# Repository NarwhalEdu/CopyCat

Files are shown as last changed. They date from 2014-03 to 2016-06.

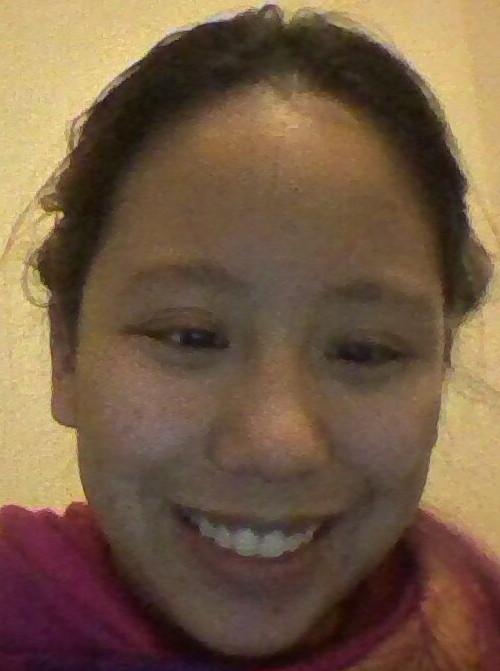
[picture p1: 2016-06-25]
vectorpaint/me.jpg

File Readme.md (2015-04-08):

NarwhalEdu CopyCat Robot (Source Files)
=========

CopyCat is a small robot arm that draws.

robot drawing nyancat 
(prototype shown)

It consists of an atmega328 microcontroller running the Arduino bootloader, three servos, a lasercut acrylic/birch box, and a 3d-printed pen holder that holds markers up to a sharpie of "fine" thickness using a set screw. 

Copycat was the physical kit paired with NarwhalEdu's first class, "Robots, Drawing, and Engineering: An Online Course," and was mailed to our kickstarter backers in February 2014. See https://www.kickstarter.com/projects/narwhaledu/robots-drawing-and-engineering-an-online-course for more information on the kickstarter.

Update (April 2015): It is accompanied by our EdX class, now released to the public for free:  https://edge.edx.org/courses/NarwhalEdu/E101/2014_Spring/info 
You will need to sign up for an Edge Edx account (any one will do).
edx screenshot

kickstarter gif

Version
----

1.0

Repository Structure
-----------

### Hardware
#### Requirements
Screwdriver, soldering iron and solder, heatshrink and hot air gun if you wish

#### Lasercut Pieces

The solidworks files are the oldest -- the folder structure may be a bit messed up as of 13 March 2014, so the assembly file may not work out of the box, but all the files are there. However, the hole sizes and other cosmetic changes may have occurred between the solidworks files and the final inkscape lasercut files.

The Lasercut-ponoko files are EXAMPLES only of how you might order the pieces from ponoko. !!We have not ordered these files from ponoko or shapeways ourselves.!!

The most accurate files, although still not fully accurate, are the inkscape .svg (exported to .pdf as well) files in Lasercut-Yubo. However, the thickness of the legs on the C and D pieces are still thinner than the final version, which has a closer-fit with piece E.

To order lasercut pieces individually, we suggest (but cannot guarantee) using inkscape to move the Yubo drawings into ponoko templates, and then filing holes that are too small or hot-gluing holes that are too big. The main reason for the uncertainty is variation in lasercutter kerf widths depending on the lasercutter, which affects the pressfits we have in our design (on the potentiometer, the servo horns, and close-fit on C/D/E pieces).

#### 3d Printed Penholder

The pen holder is 3d printed and can be ordered from shapeways. We recommend the hollow version if you are printing on shapeways, as it will save some costs.

#### Potentiometer

Additionally, one thing not shown is that we stripped and soldered the potentiometers to fit onto the I/O shield appropriately.

### Code

We'll release more code after the class ends at the end of March 2014. For now, there's some basic code up in which the servo robot arm will follow the potentiometer arm in a "copycat" configuration.

### Instructions

In the "instructions" folder you can find the bill of materials for the individual kits, complete with cost; the packing slip; and the assembly instructions. If you are building from scratch you will need not only a screwdriver but also a soldering iron and solder in order to assemble the potentiometers, which we did for the students.

Important Links
--------------
- https://www.kickstarter.com/projects/narwhaledu/robots-drawing-and-engineering-an-online-course
- http://narwhaledu.com/copycat
- http://github.com/narwhaledu/copycat

Installation
--------------
Warning: The full filesize for this repo is over 60 megabytes.

```sh
git clone [git-repo-url] copycat
cd copycat
```

License
----

Public Domain: http://creativecommons.org/publicdomain/zero/1.0/

To the extent possible under law, NarwhalEdu has waived all copyright and related or neighboring rights to CopyCat v1.0. This work is published from: United States. 

If you happen to see us in person, feel free to buy us some cheetos or tangerines.

Contact
----
opensource@narwhaledu.com

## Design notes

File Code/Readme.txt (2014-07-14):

CopyCat:
Arduino
Basic "copycat" arm functionality, using two potentiometers as inputs to control two servomotors.

basicsIK: 
Arduino
Basic inverse kinematics code, including examples of how to program a circle and a line.

paint:
Processing
A graphical user interface for drawing and sending commands over serial to a plugged-in Arduino running serialdraw.

serialdraw:
Arduino
Code to accept x,y commands from Processing and turn them into theta values so that the robot arm may draw them.

Inverse Kinematics explanation:
See trig.png, as well as
http://www.instructables.com/id/Robotic-Arm-with-Servo-Motors/step5/Plug-it-in-and-Write-some-code/
as well as
http://www.eng.utah.edu/~cs5310/chapters.html (uh oh! July 2014: Files now locked by password and not accessible)
Also.
"if this elbowup/down stuff is coming out of nowhere -- basically there are two combinations of theta 1 and theta 2 that will work for any given x,y coordinate and you just pick whether you want the elbow up or down solution)"
The code in basicIK.ino should be understandable after reading these resources.

For mapping the working envelope of the arm, please see the python file workingenv.py --> see workingenvelope.png for what the output should look like (generated using ipython).

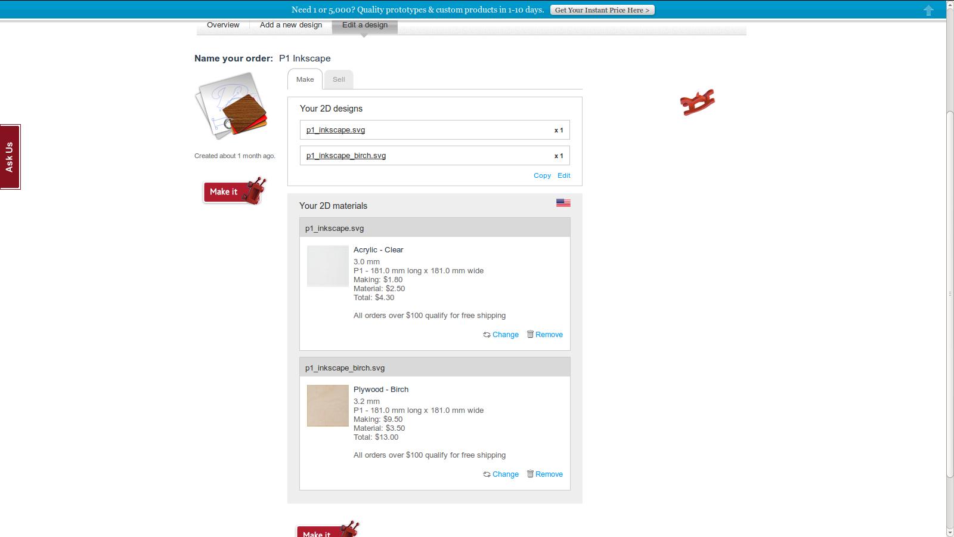
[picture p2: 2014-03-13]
Hardware/Lasercut-Ponoko-Examples/ponoko.jpg

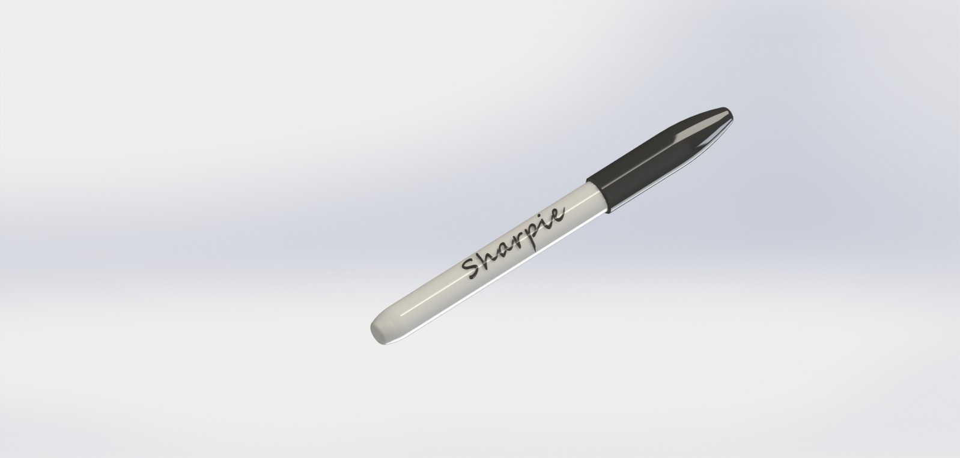
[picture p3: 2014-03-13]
Hardware/pen_holder/sharpie-brand-marker-pen/Renderings/Sharpie render20120321-19804-l9pclu.JPG

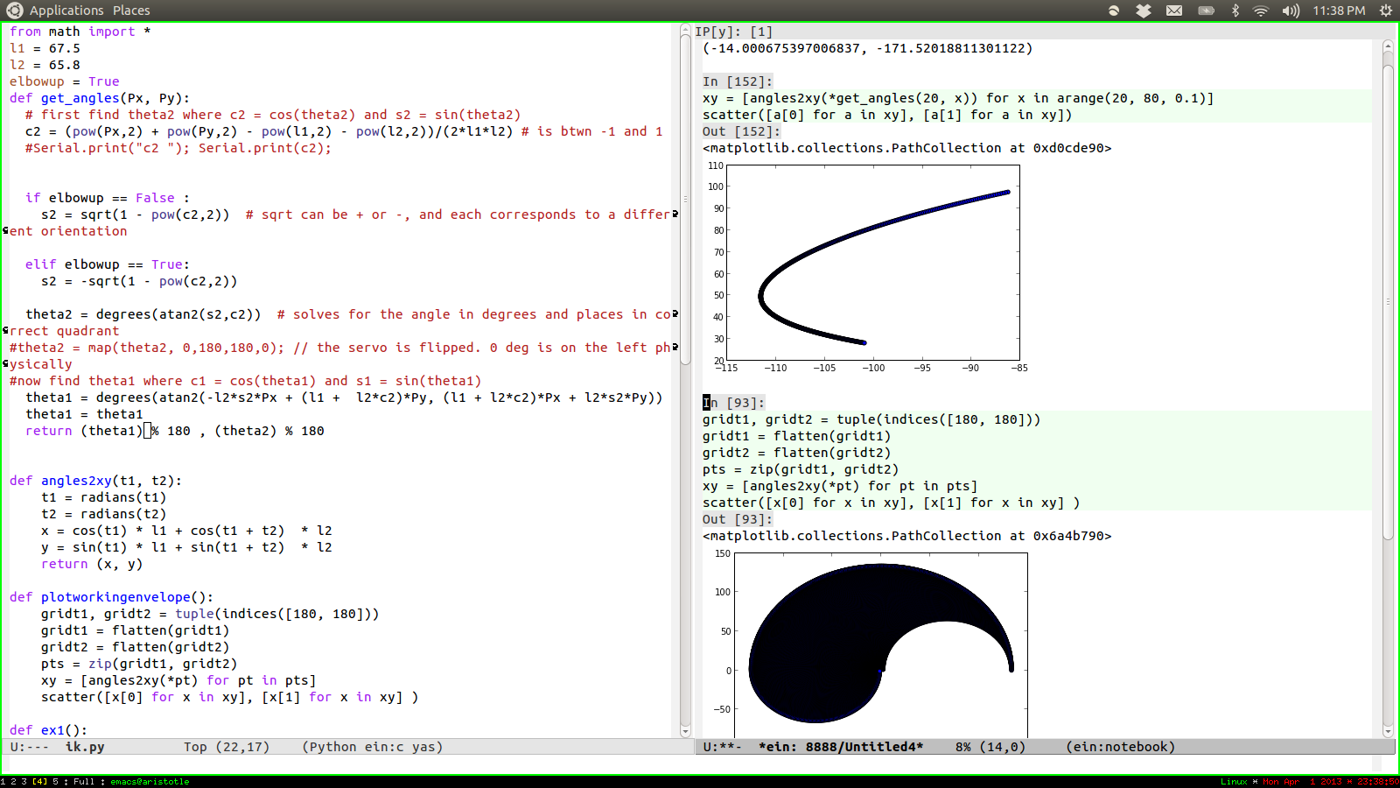
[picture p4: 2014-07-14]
Code/workingenvelope.png

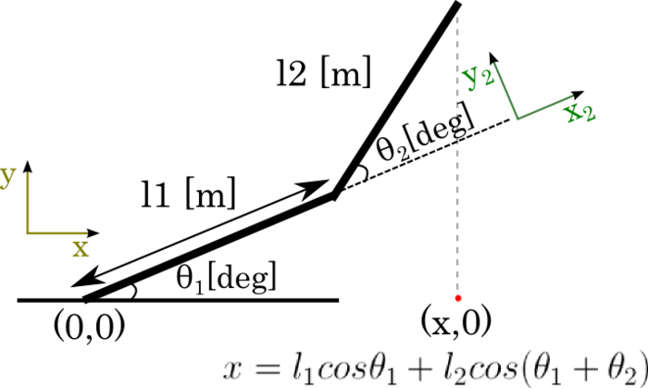
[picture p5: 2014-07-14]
Code/trig.png

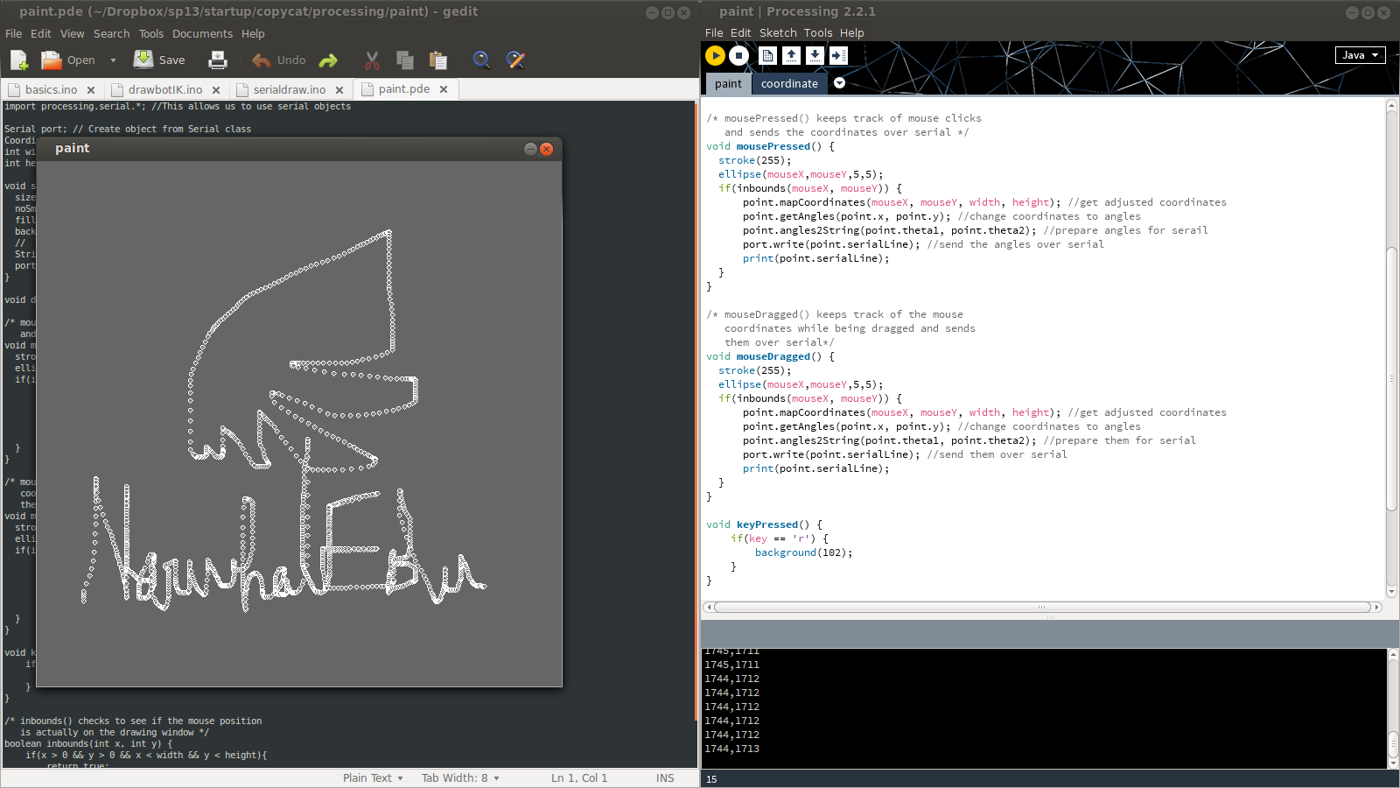
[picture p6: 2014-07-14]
Code/serialdraw+paint.png

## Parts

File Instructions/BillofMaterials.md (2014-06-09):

<table>
<col width="11%" />
<col width="11%" />
<col width="11%" />
<col width="11%" />
<col width="11%" />
<col width="11%" />
<col width="11%" />
<col width="11%" />
<col width="11%" />
<tbody>
<tr class="odd">
<td align="left"></td>
<td align="left"></td>
<td align="left"></td>
<td align="left"></td>
<td align="left"></td>
<td align="left"></td>
<td align="left"></td>
<td align="left"></td>
<td align="left"></td>
</tr>
<tr class="even">
<td align="left"><p>.</p></td>
<td align="left">what</td>
<td align="left">Supplier</td>
<td align="left">Bulk Website</td>
<td align="left">Website for Individual Kit Cost / Part number</td>
<td align="left">Cost</td>
<td align="left">Quantity needed</td>
<td align="left"></td>
<td align="left"></td>
</tr>
<tr class="odd">
<td align="left"><p>.</p></td>
<td align="left">ES08DE</td>
<td align="left">EMAX</td>
<td align="left"><a href="https://www.google.com/url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">http://www.emaxmodel.com/views.asp?hw_id=1247</a></td>
<td align="left"><a href="https://www.google.com/url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">http://www.banggood.com/Wholesale-Emax-ES08DE-Digital-Micro-Servo-For-250-450-Helis-Airplanes-p-68709.html</a></td>
<td align="left">$17.48</td>
<td align="left">4</td>
<td align="left"></td>
<td align="left"></td>
</tr>
<tr class="even">
<td align="left"><p>.</p></td>
<td align="left">ES08DE long screws</td>
<td align="left">EMAX</td>
<td align="left">not available for purchase individually</td>
<td align="left">http://www.mcmaster.com/#90380a008/=qb8znh Mcmaster part #90380A008 is roughly equivalent to the EMAX screws</td>
<td align="left">$3.50</td>
<td align="left">7 out of box of 50</td>
<td align="left"></td>
<td align="left"></td>
</tr>
<tr class="odd">
<td align="left"><p>.</p></td>
<td align="left"></td>
<td align="left"></td>
<td align="left"></td>
<td align="left"></td>
<td align="left"></td>
<td align="left"></td>
<td align="left"></td>
<td align="left"></td>
</tr>
<tr class="even">
<td align="left"><p>.</p></td>
<td align="left">Potentiometer cables</td>
<td align="left">Pololu</td>
<td align="left"><a href="https://www.google.com/url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">http://www.pololu.com/product/780</a></td>
<td align="left"></td>
<td align="left">$2.49</td>
<td align="left">1</td>
<td align="left"></td>
<td align="left"></td>
</tr>
<tr class="odd">
<td align="left"><p>.</p></td>
<td align="left"></td>
<td align="left"></td>
<td align="left"></td>
<td align="left"></td>
<td align="left"></td>
<td align="left"></td>
<td align="left"></td>
<td align="left"></td>
</tr>
<tr class="even">
<td align="left"><p>.</p></td>
<td align="left"></td>
<td align="left"></td>
<td align="left"></td>
<td align="left"></td>
<td align="left"></td>
<td align="left"></td>
<td align="left"></td>
<td align="left"></td>
</tr>
<tr class="odd">
<td align="left"><p>.</p></td>
<td align="left">Servo Extension Cable 300mm</td>
<td align="left">RobotMesh</td>
<td align="left"><a href="https://www.google.com/url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">http://www.robotmesh.com/servo-extension-cable-300mm</a></td>
<td align="left"></td>
<td align="left">$1.40</td>
<td align="left">2</td>
<td align="left"></td>
<td align="left"></td>
</tr>
<tr class="even">
<td align="left"><p>.</p></td>
<td align="left">Servo Extension Cable 150mm</td>
<td align="left">RobotMesh</td>
<td align="left"><a href="https://www.google.com/url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">http://www.robotmesh.com/servo-extension-cable-150mm</a></td>
<td align="left"></td>
<td align="left">$0.60</td>
<td align="left">1</td>
<td align="left"></td>
<td align="left"></td>
</tr>
<tr class="odd">
<td align="left"><p>.</p></td>
<td align="left"></td>
<td align="left"></td>
<td align="left"></td>
<td align="left"></td>
<td align="left"></td>
<td align="left"></td>
<td align="left"></td>
<td align="left"></td>
</tr>
<tr class="even">
<td align="left"><p>.</p></td>
<td align="left">POTENTIOMETER ROTARY 5K OHM 16MM SOLDER</td>
<td align="left">Digikey</td>
<td align="left"><a href="https://www.google.com/url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">http://www.digikey.com/product-detail/en/P160KNP-0FC25B5K/987-1311-ND/2408888</a></td>
<td align="left">987-1311-ND</td>
<td align="left">$1.68</td>
<td align="left">2</td>
<td align="left"></td>
<td align="left"></td>
</tr>
<tr class="odd">
<td align="left"><p>.</p></td>
<td align="left"></td>
<td align="left"></td>
<td align="left"></td>
<td align="left"></td>
<td align="left"></td>
<td align="left"></td>
<td align="left"></td>
<td align="left"></td>
</tr>
<tr class="even">
<td align="left"><p>.</p></td>
<td align="left">Zinc-pltd Stl Pan Head Phillips Machine Screw, 4-40 Thread, 1/2&quot; Length x 100</td>
<td align="left">Mcmaster</td>
<td align="left"><a href="https://www.google.com/url?q=http://mcmaster.com&amp;usd=2&amp;usg=ALhdy2_r-PfuAHiMmXkCKGf9Mx1Ry3E_oQ">mcmaster.com</a></td>
<td align="left">90272A110</td>
<td align="left">$1.63</td>
<td align="left">13 needed out of box of 100</td>
<td align="left"></td>
<td align="left"></td>
</tr>
<tr class="odd">
<td align="left"><p>.</p></td>
<td align="left">Zinc-plated Steel Machine Screw Hex Nut, 4-40 Thread Size, 1/4&quot; Width, 3/32&quot; Height x 100</td>
<td align="left">Mcmaster</td>
<td align="left"><a href="https://www.google.com/url?q=http://mcmaster.com&amp;usd=2&amp;usg=ALhdy2_r-PfuAHiMmXkCKGf9Mx1Ry3E_oQ">mcmaster.com</a></td>
<td align="left">90480A005</td>
<td align="left">$0.81</td>
<td align="left">21 needed out of box of 100</td>
<td align="left"></td>
<td align="left"></td>
</tr>
<tr class="even">
<td align="left"><p>.</p></td>
<td align="left">Zinc-Plated Steel Type A SAE Flat Washer, Number 2 Screw Size, 7/32&quot; OD, .01&quot;-.03&quot; Thick</td>
<td align="left">Mcmaster</td>
<td align="left"><a href="https://www.google.com/url?q=http://mcmaster.com&amp;usd=2&amp;usg=ALhdy2_r-PfuAHiMmXkCKGf9Mx1Ry3E_oQ">mcmaster.com</a></td>
<td align="left">90126A501</td>
<td align="left">$1.19</td>
<td align="left">1 needed out of box of 100</td>
<td align="left"></td>
<td align="left"></td>
</tr>
<tr class="odd">
<td align="left"><p>.</p></td>
<td align="left"></td>
<td align="left"></td>
<td align="left"></td>
<td align="left"></td>
<td align="left"></td>
<td align="left"></td>
<td align="left"></td>
<td align="left"></td>
</tr>
<tr class="even">
<td align="left"><p>.</p></td>
<td align="left">birch pieces</td>
<td align="left">Ponoko Lasercut Quote</td>
<td align="left"><a href="https://www.google.com/url?q=http://ponoko.com&amp;usd=2&amp;usg=ALhdy29cn-jdru5WrcO2noldjQy0oRjBWA">ponoko.com</a></td>
<td align="left"></td>
<td align="left">$13.00</td>
<td align="left"></td>
<td align="left"></td>
<td align="left"></td>
</tr>
<tr class="odd">
<td align="left"><p>.</p></td>
<td align="left">acrylic pieces</td>
<td align="left">Ponoko Lasercut Quote</td>
<td align="left"><a href="https://www.google.com/url?q=http://ponoko.com&amp;usd=2&amp;usg=ALhdy29cn-jdru5WrcO2noldjQy0oRjBWA">ponoko.com</a></td>
<td align="left"></td>
<td align="left">$4.30</td>
<td align="left"></td>
<td align="left"></td>
<td align="left"></td>
</tr>
<tr class="even">
<td align="left"><p>.</p></td>
<td align="left"></td>
<td align="left"></td>
<td align="left"></td>
<td align="left"></td>
<td align="left"></td>
<td align="left"></td>
<td align="left"></td>
<td align="left"></td>
</tr>
<tr class="odd">
<td align="left"><p>.</p></td>
<td align="left">3d print pen holder</td>
<td align="left">Shapeways Quote</td>
<td align="left"><a href="https://www.google.com/url?q=http://shapeways.com&amp;usd=2&amp;usg=ALhdy2_YYUwusA8m6Woy5YYOLUOF8yBiEw">shapeways.com</a></td>
<td align="left"></td>
<td align="left">$7.30</td>
<td align="left"></td>
<td align="left"></td>
<td align="left"></td>
</tr>
<tr class="even">
<td align="left"><p>.</p></td>
<td align="left"></td>
<td align="left"></td>
<td align="left"></td>
<td align="left"></td>
<td align="left"></td>
<td align="left"></td>
<td align="left"></td>
<td align="left"></td>
</tr>
<tr class="odd">
<td align="left"><p>.</p></td>
<td align="left">Nano carrier Board</td>
<td align="left">iTeadstudio</td>
<td align="left"><a href="https://www.google.com/url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">http://imall.iteadstudio.com/im120417016.html</a></td>
<td align="left"></td>
<td align="left">$9.90</td>
<td align="left"></td>
<td align="left"></td>
<td align="left"></td>
</tr>
<tr class="even">
<td align="left"><p>.</p></td>
<td align="left">Micro USB</td>
<td align="left">iTeadstudio</td>
<td align="left"><a href="https://www.google.com/url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">http://imall.iteadstudio.com/im130416001.html</a></td>
<td align="left"></td>
<td align="left">$1.20</td>
<td align="left"></td>
<td align="left"></td>
<td align="left"></td>
</tr>
<tr class="odd">
<td align="left"><p>.</p></td>
<td align="left">7.5V 1A wallwart</td>
<td align="left">iTeadstudio</td>
<td align="left"><a href="https://www.google.com/url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">http://imall.iteadstudio.com/power/im120718002.html</a></td>
<td align="left"></td>
<td align="left">$2.90</td>
<td align="left"></td>
<td align="left"></td>
<td align="left"></td>
</tr>
<tr class="even">
<td align="left"><p>.</p></td>
<td align="left">Nano microcontroller</td>
<td align="left">iTeadstudio</td>
<td align="left"><a href="https://www.google.com/url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">http://imall.iteadstudio.com/development-platform/arduino/im130615004.html</a></td>
<td align="left"></td>
<td align="left">$5.00</td>
<td align="left"></td>
<td align="left"></td>
<td align="left"></td>
</tr>
<tr class="odd">
<td align="left"><p>.</p></td>
<td align="left"></td>
<td align="left"></td>
<td align="left"></td>
<td align="left"></td>
<td align="left"></td>
<td align="left"></td>
<td align="left"></td>
<td align="left"></td>
</tr>
<tr class="even">
<td align="left"><p>.</p></td>
<td align="left">Boxes</td>
<td align="left">ULINE</td>
<td align="left"><a href="https://www.google.com/url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">http://www.uline.com/Product/Detail/S-16947/Indestructo-Literature-Mailers/10-x-4-x-4-White-Tab-Locking-Literature-Mailers</a></td>
<td align="left"></td>
<td align="left"></td>
<td align="left">These cost $0.92 each (if bought in quantity 50)</td>
<td align="left"></td>
<td align="left"></td>
</tr>
<tr class="odd">
<td align="left"><p>.</p></td>
<td align="left"></td>
<td align="left"></td>
<td align="left"></td>
<td align="left"></td>
<td align="left"></td>
<td align="left"></td>
<td align="left"></td>
<td align="left"></td>
</tr>
<tr class="even">
<td align="left"><p>.</p></td>
<td align="left">#1 Screwdriver</td>
<td align="left">any hardware store</td>
<td align="left"></td>
<td align="left"></td>
<td align="left">$1.00</td>
<td align="left"></td>
<td align="left"></td>
<td align="left"></td>
</tr>
<tr class="odd">
<td align="left"><p>.</p></td>
<td align="left"></td>
<td align="left"></td>
<td align="left"></td>
<td align="left"></td>
<td align="left"></td>
<td align="left"></td>
<td align="left"></td>
<td align="left"></td>
</tr>
<tr class="even">
<td align="left"><p>.</p></td>
<td align="left"></td>
<td align="left"></td>
<td align="left"></td>
<td align="left"></td>
<td align="left"></td>
<td align="left">Direct cost (NOT including shipping):</td>
<td align="left">40% profit model, aka 66% markup:</td>
<td align="left">See: http://www.longtail.com/the_long_tail/2009/01/a-business-mode.html</td>
</tr>
<tr class="odd">
<td align="left"><p>.</p></td>
<td align="left"></td>
<td align="left"></td>
<td align="left"></td>
<td align="left"></td>
<td align="left"></td>
<td align="left">$75.38</td>
<td align="left">$125.1308</td>
<td align="left"></td>
</tr>
</tbody>
</table>

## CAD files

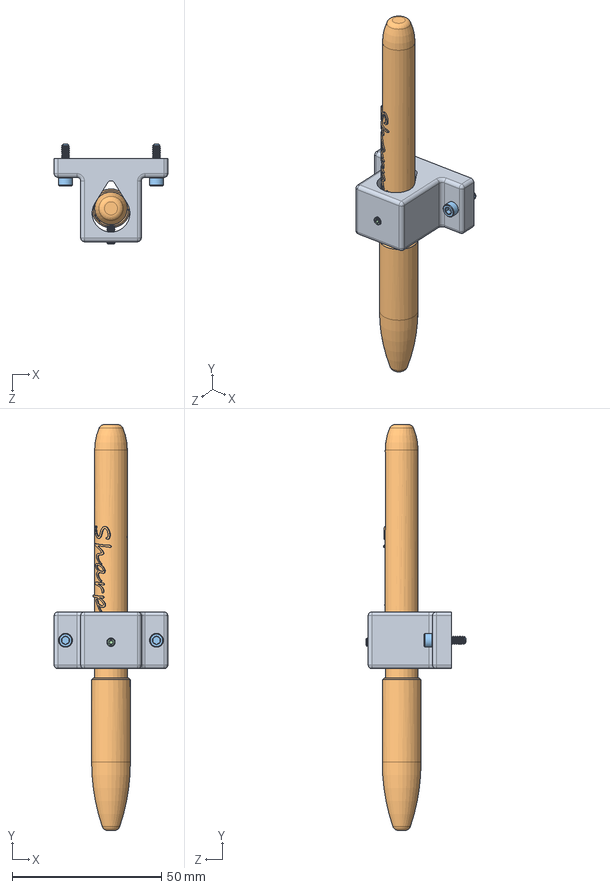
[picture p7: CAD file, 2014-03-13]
Hardware/pen_holder/pen_holder_assembly.SLDASM
38.1 x 136.0 x 33.4 mm
pen_holder
Sharpie Marker v1.0
4-40x0.4375_thumbscrew x 2
4-40x.25 set screw

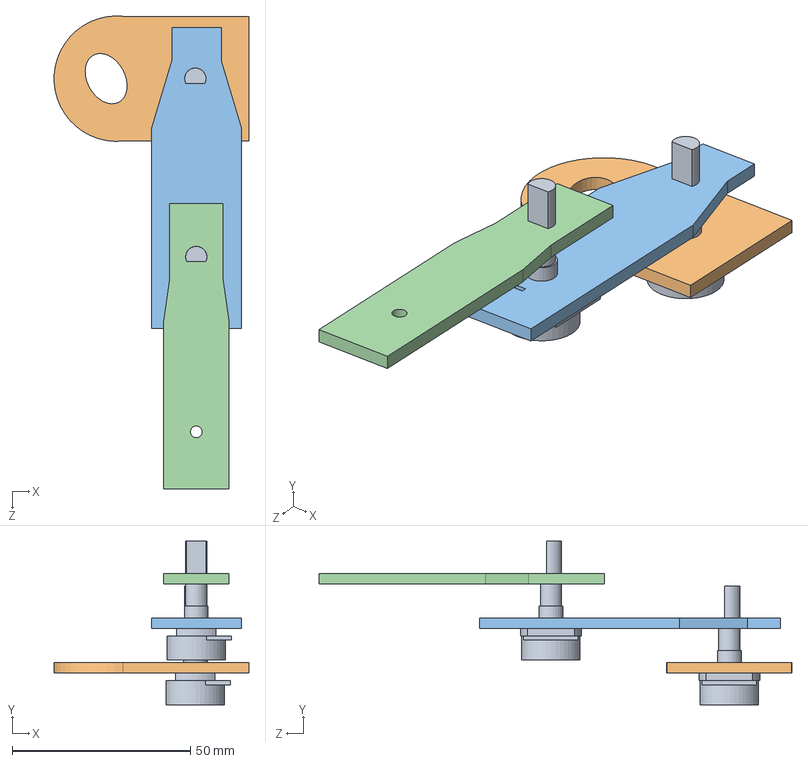
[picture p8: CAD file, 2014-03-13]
Hardware/Solidworks/potarm-Assem.SLDASM
54.6 x 45.8 x 132.6 mm
pot x 2
potbase
l1-pot
l2-pot

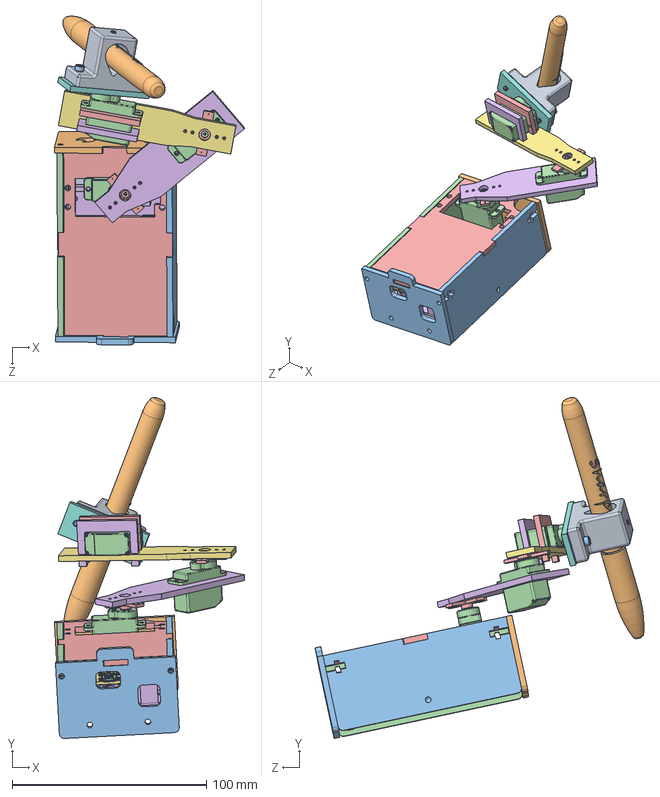
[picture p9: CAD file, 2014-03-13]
Hardware/Solidworks/Assem2.SLDASM
97.9 x 175.6 x 169.4 mm
box_bottom
4-40 Standoff 1_4 x 3
box_sides3
box_sides4
box_lid
iteadboard
nano-board
2pin_header__02 x 3
15pin_header__ x 2
atmega328
ftdi FT232rl
smt_resistor222 x 5
led x 4
16mhz crystal - measured
MINIUSBSHELL
MINIUSBCORE
MINI USB CONTACT x 5
MINI USB SOLDER
cap106C x 2
reset core
reset shell
nano - reg
NANO DIODE
189 RESISTOR PACK
102 RESISTOR PACK
box_front2
box_back2
Emax ES08A x 3
cross-horn x 2
l1
l2
penpiece
pen_holder
Sharpie Marker v1.0
4-40x0.4375_thumbscrew x 2
4-40x.25 set screw
ubracket-holes
ubracket-noholes

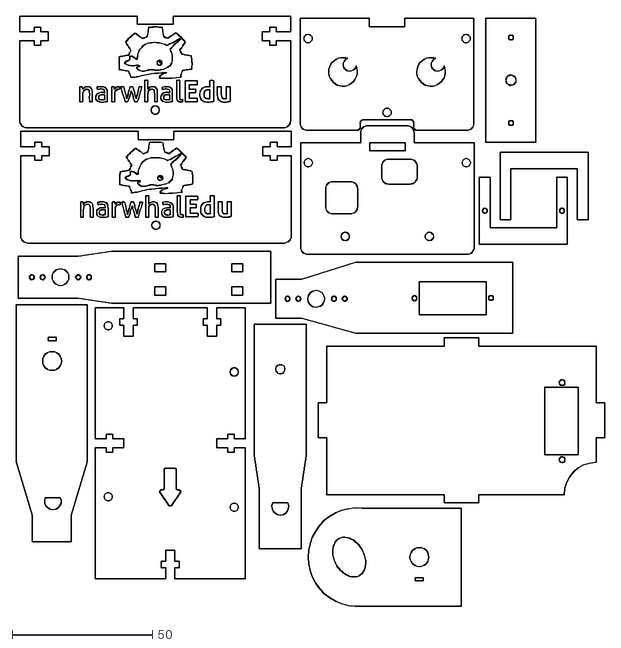
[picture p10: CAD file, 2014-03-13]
Hardware/DXF/allparts.DXF
209.7 x 211.1

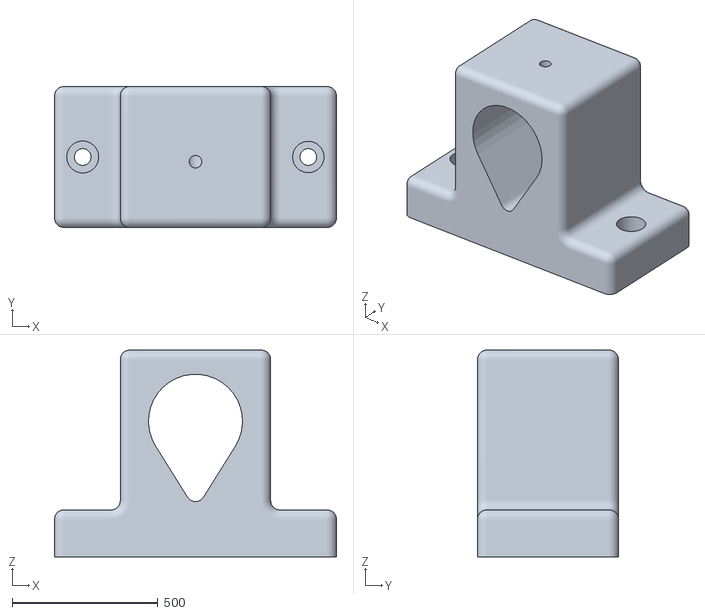
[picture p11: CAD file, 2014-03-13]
Hardware/pen_holder/penholderhollow_fixed.stl
967.7 x 483.9 x 709.7

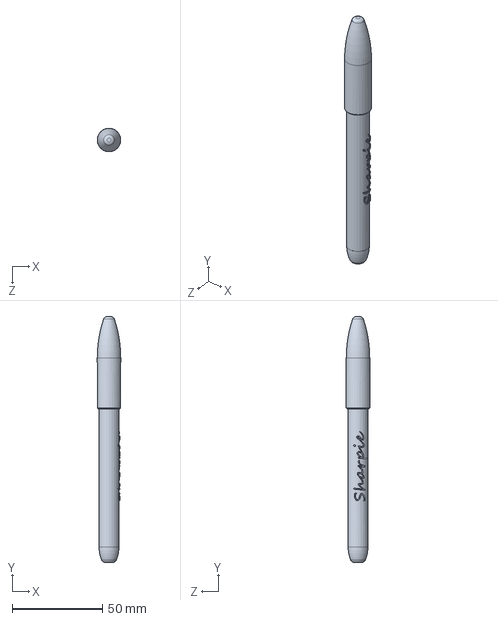
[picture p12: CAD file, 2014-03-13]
Hardware/pen_holder/sharpie-brand-marker-pen/Sharpie Marker v1.0.SLDPRT
13.0 x 136.0 x 13.0 mm

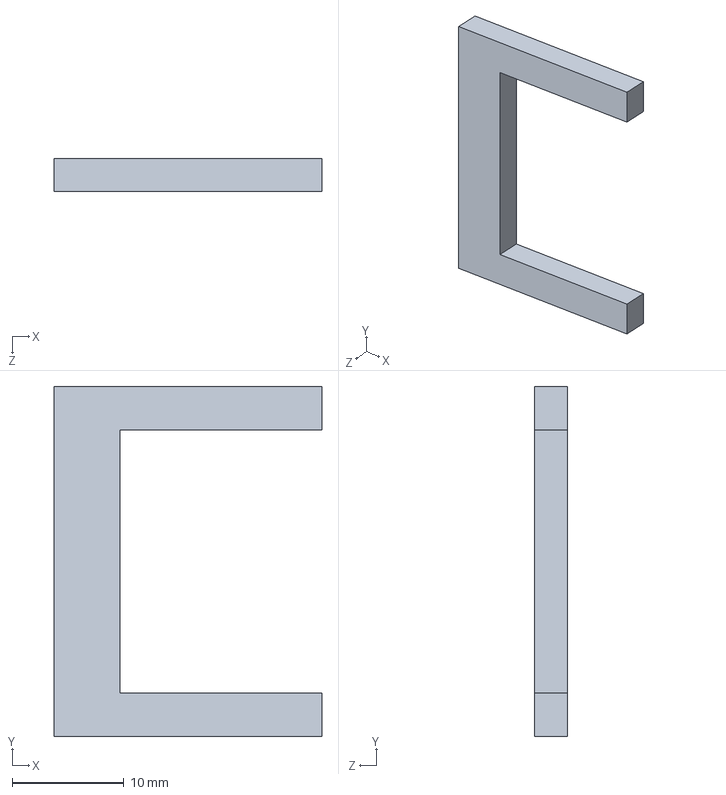
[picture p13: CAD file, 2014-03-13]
Hardware/Solidworks/ubracket-noholes.SLDPRT
24.0 x 31.4 x 3.00 mm

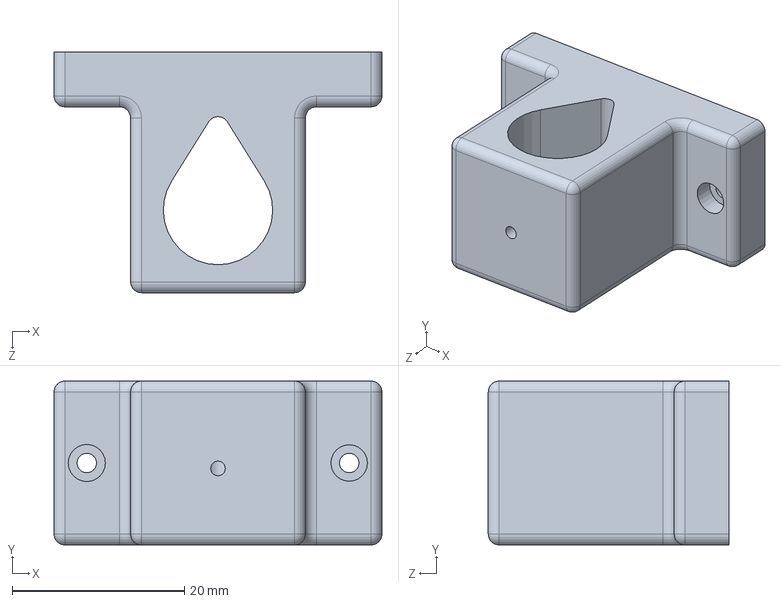
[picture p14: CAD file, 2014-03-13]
Hardware/pen_holder/pen_holder.SLDPRT
38.1 x 19.1 x 27.9 mm

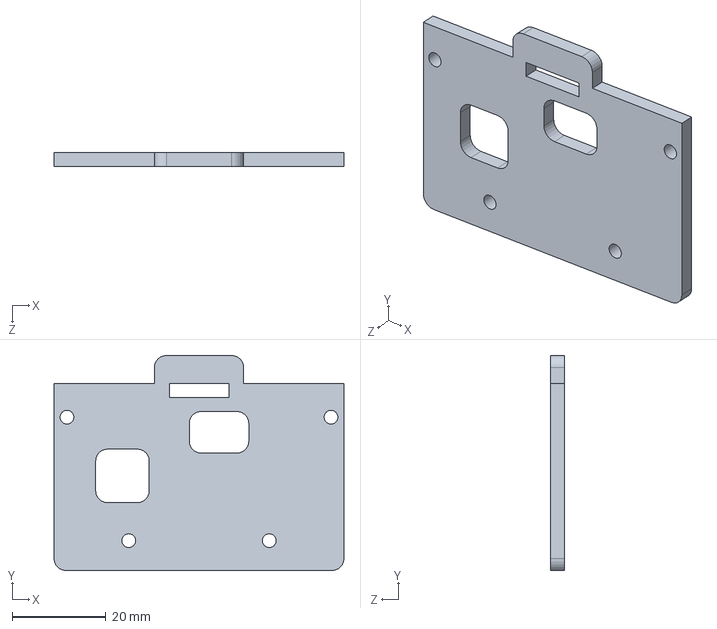
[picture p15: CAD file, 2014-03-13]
Hardware/Solidworks/box_back2.SLDPRT
61.9 x 45.9 x 3.00 mm

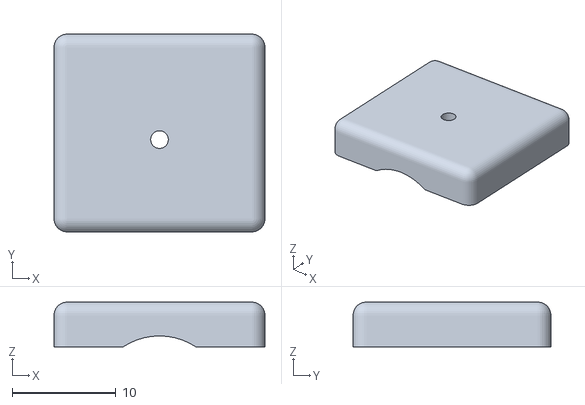
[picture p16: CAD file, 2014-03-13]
Hardware/pen_holder/pen_holder_top.STL
20.3 x 19.1 x 4.32

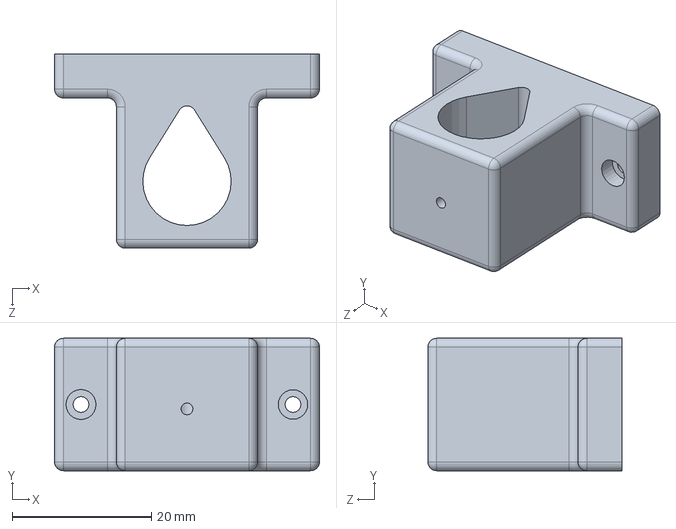
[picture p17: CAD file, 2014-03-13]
Hardware/pen_holder/pen_holder_hollow.SLDPRT
38.1 x 19.1 x 27.9 mm

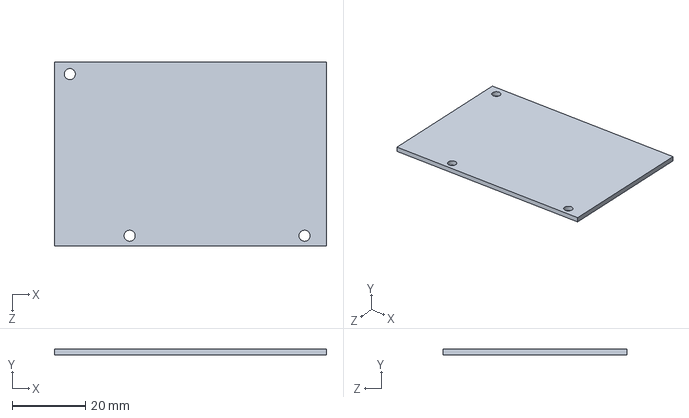
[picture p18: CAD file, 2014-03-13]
Hardware/Solidworks/io_board.SLDPRT
74.4 x 1.60 x 50.3 mm

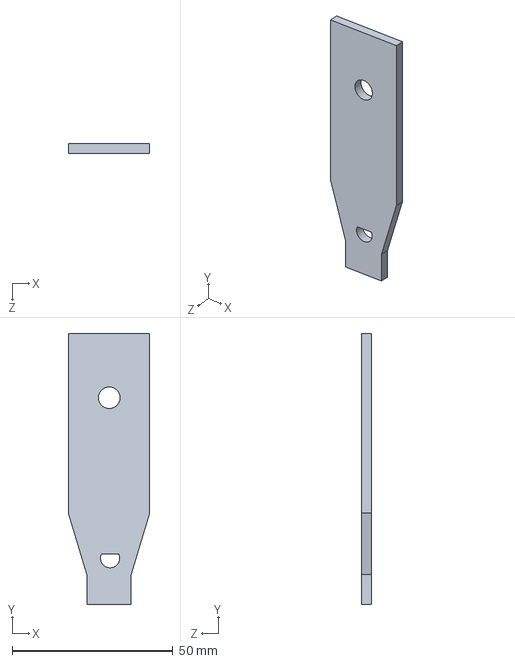
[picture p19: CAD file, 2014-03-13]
Hardware/Solidworks/l1-pot.SLDPRT
25.3 x 84.4 x 3.00 mm

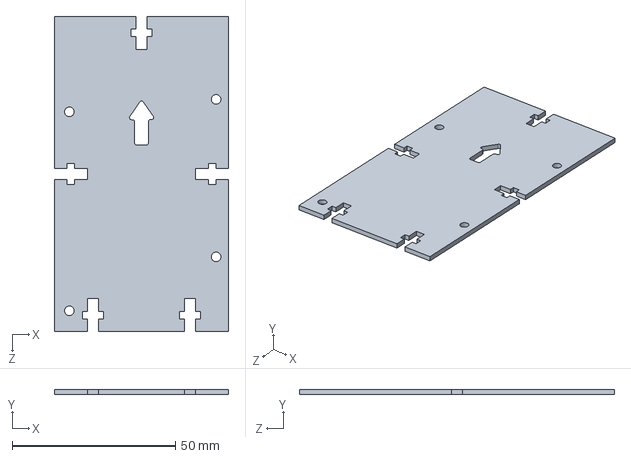
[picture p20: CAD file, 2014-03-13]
Hardware/Solidworks/box_bottom.SLDPRT
53.3 x 1.60 x 96.5 mm

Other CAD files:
Hardware/Solidworks/ubracket-holes.SLDPRT
Hardware/pen_holder/penholder_fixed.stl
Hardware/Solidworks/potbase.SLDPRT
Hardware/Solidworks/l2.SLDPRT
Hardware/DXF/box_back2.DXF
Hardware/DXF/box_bottom.DXF
Hardware/DXF/box_front2.DXF
Hardware/DXF/box_lid.DXF
Hardware/DXF/box_sides2.DXF
Hardware/DXF/box_sides3.DXF
Hardware/DXF/box_sides4.DXF
Hardware/DXF/l1-pot.DXF
Hardware/DXF/l1.DXF
Hardware/DXF/l2-pot.DXF
Hardware/DXF/l2.DXF
Hardware/DXF/penpiece.DXF
Hardware/DXF/potbase.DXF
Hardware/DXF/ubracket-holes.DXF
Hardware/DXF/ubracket-noholes.DXF
Hardware/Solidworks/box_front2.SLDPRT
Hardware/Solidworks/box_lid.SLDPRT
Hardware/Solidworks/box_sides2.SLDPRT
Hardware/Solidworks/box_sides3.SLDPRT
Hardware/Solidworks/box_sides4.SLDPRT
Hardware/Solidworks/l1.SLDPRT
Hardware/Solidworks/l2-pot.SLDPRT
Hardware/Solidworks/penpiece.SLDPRT
Hardware/pen_holder/pen_holder.STL
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

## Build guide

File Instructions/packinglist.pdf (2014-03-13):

# NarwhalEdu

accessible engineering kits and curricula

CopyCat: Drawing Robot Arm Kit

Dear Kickstarter Backer,
Thank you for joining us in exploring the wonderful world of engineering. Enclosed you should find all the parts for building a CopyCat drawing robot arm. Please check that the contents of your box match the list below. Please email support@narwhaledu.com if there are any discrepancies.

Packing List
Screwdriver
3D Printed Penholder
Washable Marker
Bolts Bag (see right)

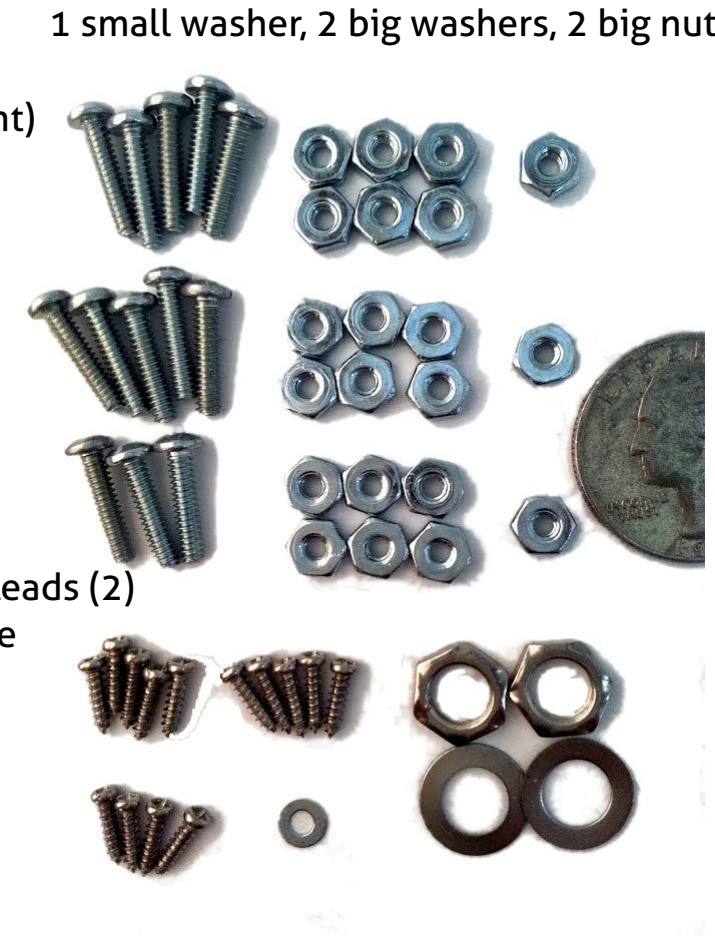
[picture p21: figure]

Lasercut Pieces Bag (see right)

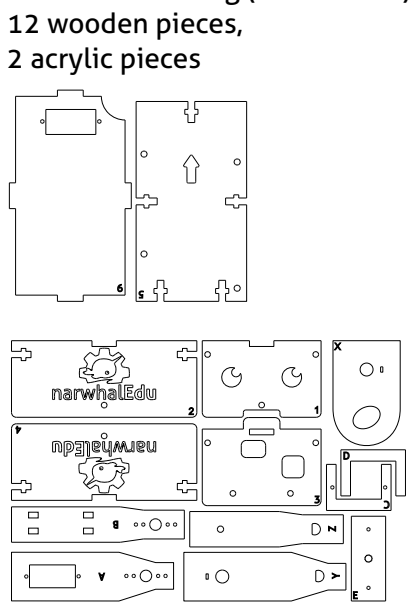
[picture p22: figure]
12 wooden pieces, 2 acrylic pieces

iTead Nano
iTead I/O Shield
iTead Wall Power Supply
iTead USB cable

EMAX ES08DE Servos (4)
Extension Cable 300m (2)
Extension Cable 150m
Potentiometer w/ soldered leads (2) Leads: White wire should be
in the middle

Assembly instructions and a parts list with more detailed information can be found at <http://narwhaledu.com/copycat>. We recommend not assembling the kit until the course begins on February 28th, 2014. You will be sent an invitation to join the course to the email you provided in the kickstarter survey around noon EST on that day. Please keep the box for storing your assembled kit and other supplies, or recycle it.

Thanks and happy roboting!
--Cappie and Nancy
Feb 5th, 2014

Website: narwhaledu.com
General Email: narwhaledu@gmail.com

Bolts Bag (close to 1:1 scale)
14 screws, 13 bolts, 21 small nuts,
1 small washer, 2 big washers, 2 big nuts

Lasercut Pieces Bag (not to scale)

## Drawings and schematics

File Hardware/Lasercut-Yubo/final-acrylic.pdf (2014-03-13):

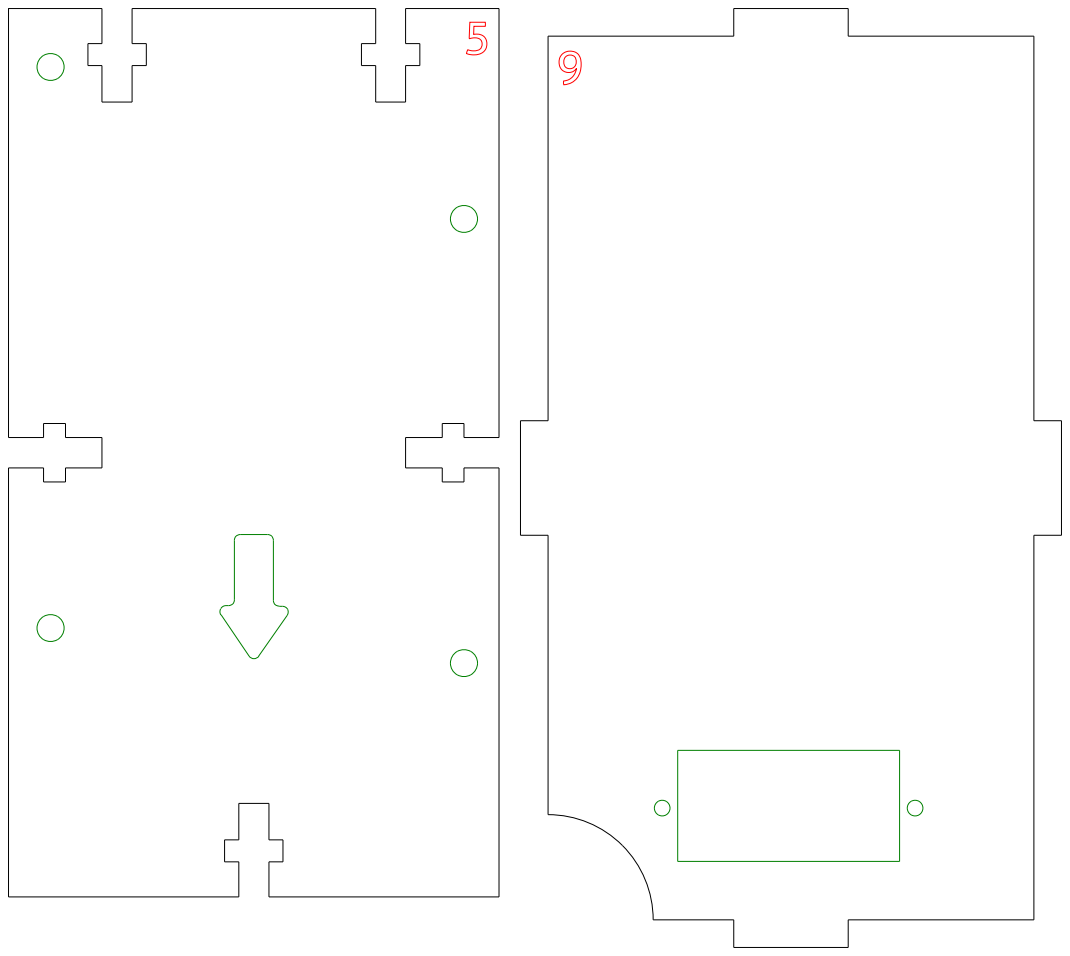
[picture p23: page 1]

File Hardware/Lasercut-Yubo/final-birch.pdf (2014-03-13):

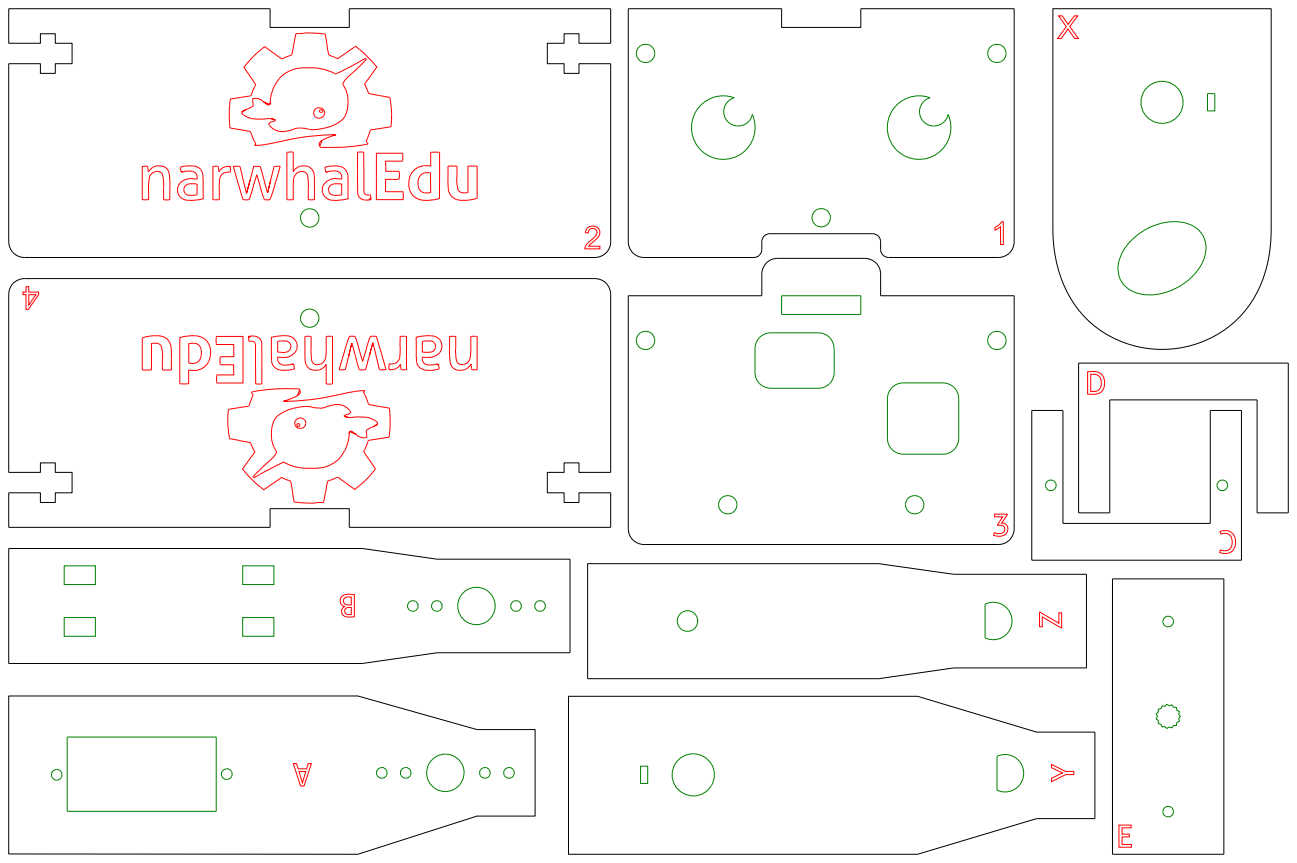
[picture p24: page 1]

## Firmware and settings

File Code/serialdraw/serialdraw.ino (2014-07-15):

// code derived from http://www.instructables.com/id/Robotic-Arm-with-Servo-Motors/?ALLSTEPS
// code derived from http://www.instructables.com/id/Intro-and-what-youll-need/?ALLSTEPS
// derived from http://arduino.cc/en/Tutorial/Graph
// code derived from http://www.circuitsathome.com/mcu/robotic-arm-inverse-kinematics-on-arduino
//l1 67.5 mm
//l2 65.8mm

#include <Servo.h>
Servo servo1;
Servo servo2;
Servo servo3;
int theta1;  // target angles as determined through IK
int theta2;
int theta1prev; //old targets for error correction
int theta2prev;
int buf;
unsigned long time; //time is really long!
int writingposition = 140;
int idleposition = 170;

void setup() {
  Serial.begin(9600);
  servo1.attach(2,750,2200);
  servo2.attach(3,750,2200);
  servo3.attach(4,750,2200);
  servo1.write(90);
  servo2.write(80);
  servo3.write(idleposition);
  pinMode(13,OUTPUT);
}
  
void loop() {
  if(Serial.available() > 0) { //check for data
    readAngles(); //get the angles
    if(theta1 > 180 || theta1 < 0) { these two if statements check if the data is reasonable.  When using drag in processing sometimes absurd numbers get sent
      theta1 = theta1prev;
    }
    if(theta2 > 180 || theta2 < 0) {
      theta2 = theta2prev;
    }
    drive_joints();
    if(!writing()){
      startWritingNow();
    }
    theta1prev = theta1;
    theta2prev = theta2;
    time = millis();
  } else if(millis() - time > 300 && writing) { //move the pen(servo3) up when done
    stopWritingNow();
  }
}

/* drive_joints() simply moves servos 1 and 2 */
void drive_joints() {
  servo1.writeMicroseconds(theta1);
  servo2.writeMicroseconds(theta2);
}

/* readAngles() reads the doubles from the serial port
   it is inteded to take in data of the form 2.2,3.4'\n'
   where there is only one decimal place and the values
   are sperated by a comma and a newline after the tuple*/   
void readAngles() {
  byte character = Serial.read(); //read the first byte on serial
  while(character != 10) {
    if(character != ','){ //newline(10) and comma are special
      buf = buf*10;
      buf += (int)(character - '0'); //these two lines turn the string into an integer
    } else if(character == ',') {
      theta1 = buf; //after a comma the buffer has the first angle
      Serial.print(theta1);
      buf = 0;
    } else {
      //      theta2 = buf; //after a newline the buffer has the second angle
      buf = 0;
    }
    while(Serial.available() == 0) {
      delayMicroseconds(100);
    }
    character = Serial.read();
  }
  theta2 = buf;
  Serial.print(",");
  Serial.println(theta2);
  buf = 0;
}

/* startWritingNow() moves servo3 into writing position
   there is a delay to wait for the other servos to get
   into position before it makes a mark */
void startWritingNow() {
  servo3.write(writingposition);
}

/* stopWritingNow() moves servo3 off the page */
void stopWritingNow() {
  servo3.write(idleposition);
}

boolean writing() {
  if(abs(servo3.read() - writingposition) < 1) {
    return true;
  } else {
    return false;
  }
}

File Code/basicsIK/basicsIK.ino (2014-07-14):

#include <Servo.h>

Servo servo1;
Servo servo2;
Servo servo3;
double l1 = 73;
double l2 = 100;
double theta1;
double theta2;
double c2;
double s2;
int writingposition = 130;
int idleposition = 110;

void setup () {
  Serial.begin(9600);
  servo1.attach(3,544,2400);
  servo2.attach(4,544,2400);
  servo3.attach(2,544,2400);
  servo3.write(idleposition);
}

void loop () {
  //line(-90,-60,50);
  circle();
  servo3.write(idleposition);
  delay(500);
}

void getAngles(float Px, float Py) {
  // first find theta2 where c2 = cos(theta2) and s2 = sin(theta2)
  c2 = (pow(Px,2) + pow(Py,2) - pow(l1,2) - pow(l2,2))/(2*l1*l2); //is btwn -1 and 1
  s2 = sqrt(1 - pow(c2,2));  //sqrt can be + or -, and each corresponds to a different orientation
  theta2 = degrees(atan2(s2,c2));  // solves for the angle in degrees and places in correct quadrant
  theta1 = degrees(atan2(-l2*s2*Px + (l1 +  l2*c2)*Py, \
                         (l1 + l2*c2)*Px + l2*s2*Py));
}

void line(int low, int high, int constY) {
  getAngles(low, constY);
  moveArms();
  delay(500);
  servo3.write(writingposition);
  for(int x=low; x<high; x++) {
    getAngles(x, constY);
    moveArms();
  }
  /* for(int x=high; x>low; x--) { */
  /*   getAngles(x, constY); */
  /*   moveArms(); */
  /* } */
}

void moveArms() {
  Serial.print(theta1);
  Serial.print(",");
  Serial.println(theta2);
  servo1.write(theta1);
  servo2.write(theta2);
  delay(30); 
}

void circle()
{
  float RADIUS = 10.0;
  //float angle = 0;
  float xaxis,yaxis,i;
  getAngles(-70, 60);
  moveArms();
  delay(500);
  servo3.write(writingposition);
  for (i = 0; i < 2 * 3.1416; i += .1) {
    xaxis = -70 + sin(i) * RADIUS;
    yaxis = 50 + cos(i) * RADIUS;
    getAngles(xaxis, yaxis);
    moveArms();
  }
}

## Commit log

2014-03-13 v1.0 files released into the wild as public domain
    [Assem2.SLDASM, Sharpie Marker v1.0.SLDPRT, allparts.DXF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]
2014-06-09 converted bill of materials to github rendered thing
